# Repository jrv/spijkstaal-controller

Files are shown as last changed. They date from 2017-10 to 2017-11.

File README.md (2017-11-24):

# spijkstaal-controller
DC motor controller, 3-5KW / 24V

Experimental design for a replacement motor controller for a 1980's Spijkstaal electric vehicle.
This design is made in KiCad

Designed for a 24V Lead-Acid battery and a 3KW, 24V DC motor

Traditional H-bridge design with an Arduino as controlling interface.
The high power print and the controller print are seperate.

Carefull, this is work in progress. As it is now, it's sure to give you 
spectacular fireworks, but no moving vehicle!

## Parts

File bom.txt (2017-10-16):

BOM Mosfet board
================
8 x bout, 16x moer, 24xring M6 (€30,- montagetechniek.nl)
4 x 10K of 100K weerstand (naar 0 trekken)
1 x  RS 189-6256
1 x  RS 189-6060
12 x PSMN3R4-30PL Mosfet
5 x IDP30E65D1XKSA1
1 x Pudenz 425A Automotive Bolt-down Fuse, 80V dc
2 x 2200uF / 35V Elco
12 x Weerstand 4.7 ohm, 1/2Watt

BOM Arduino board
=================
Pin headers (arduino)
2 x DIP 2x8 voet
2 x 4u7 / 60V
5 x 100uF
1 x 7805
1 x 2200uF
1 x 1N4007
1 x RS 820-1576 pin header
1 x RS 820-1633 connector housing
1 x 7815ACT
2 x 1N5819
2 x IR2184
1 x Fuse holder RS  176-9047

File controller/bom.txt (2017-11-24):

Farnell:

2325975		1x	Fast / Ultrafast Diode 600V, 200A	23,38
2784061		4x	IXFN360N10T BJT MostFet 360A/100V	19,10
		    4x  Infineon IDP30E65D1 Disode 
2762031		1x	Fuse 150A 				14,34
2468299		2x	Condensator 2200 uF/100V		 3,13

RS: 
784-6229	1x	MagnaChip Dual Diode 400V 200A		19,43
125-8041	4x	IXFN360N10T BJT MostFet 360A/100V	18,77
787-4394	1x	LittleFuse 150A 32V fuse		 6,19
744-1183	2x 	Condensator 2200 uF/100V		 3,79

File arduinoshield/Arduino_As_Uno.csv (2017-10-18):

Id | Designator | Package | Quantity | Designation | Supplier and ref
1 | P1 | Socket_Strip_Arduino_1x08 | 1 | Power
2 | P2 | Socket_Strip_Arduino_1x06 | 1 | Analog
3 | P3 | Socket_Strip_Arduino_1x10 | 1 | Digital
4 | P4 | Socket_Strip_Arduino_1x08 | 1 | Digital
5 | P5,P6,P7,P8 | Arduino_1pin | 4 | CONN_01X01
6 | C6,C8 | CP_Radial_D5.0mm_P2.00mm | 2 | 4u7
7 | F1 | Fuseholder5x20_horiz_open_Schurter_0031_8201 | 1 | 1A
8 | R2,R4,R5 | R_1206_HandSoldering | 3 | 10K
9 | R3 | R_1206_HandSoldering | 1 | 4K7
10 | C1 | CP_Radial_D13.0mm_P5.00mm | 1 | 2200uF
11 | C2,C4,C5,C7,C9 | C_1206_HandSoldering | 5 | 100nF
12 | D1 | D_2114 | 1 | MRA4007T3G
13 | D2,D3 | D_SOD-123 | 2 | 1N5819HW-7-F
14 | U1 | ATPAK-2 | 1 | MC7815BD2TR4G
15 | U2 | ATPAK-2 | 1 | L7805CD2T-TR
16 | U3,U4 | SOIC-8-N | 2 | IR2184SPBF
17 | J1 | JST_XH_B08B-XH-A_08x2.50mm_Straight | 1 | Conn_01x08
18 | J2 | JST_XH_B05B-XH-A_05x2.50mm_Straight | 1 | Conn_01x05
19 | J3,J4,J6,J7 | JST_XH_B02B-XH-A_02x2.50mm_Straight | 4 | Conn_01x02
20 | J5 | JST_XH_B03B-XH-A_03x2.50mm_Straight | 1 | Conn_01x03

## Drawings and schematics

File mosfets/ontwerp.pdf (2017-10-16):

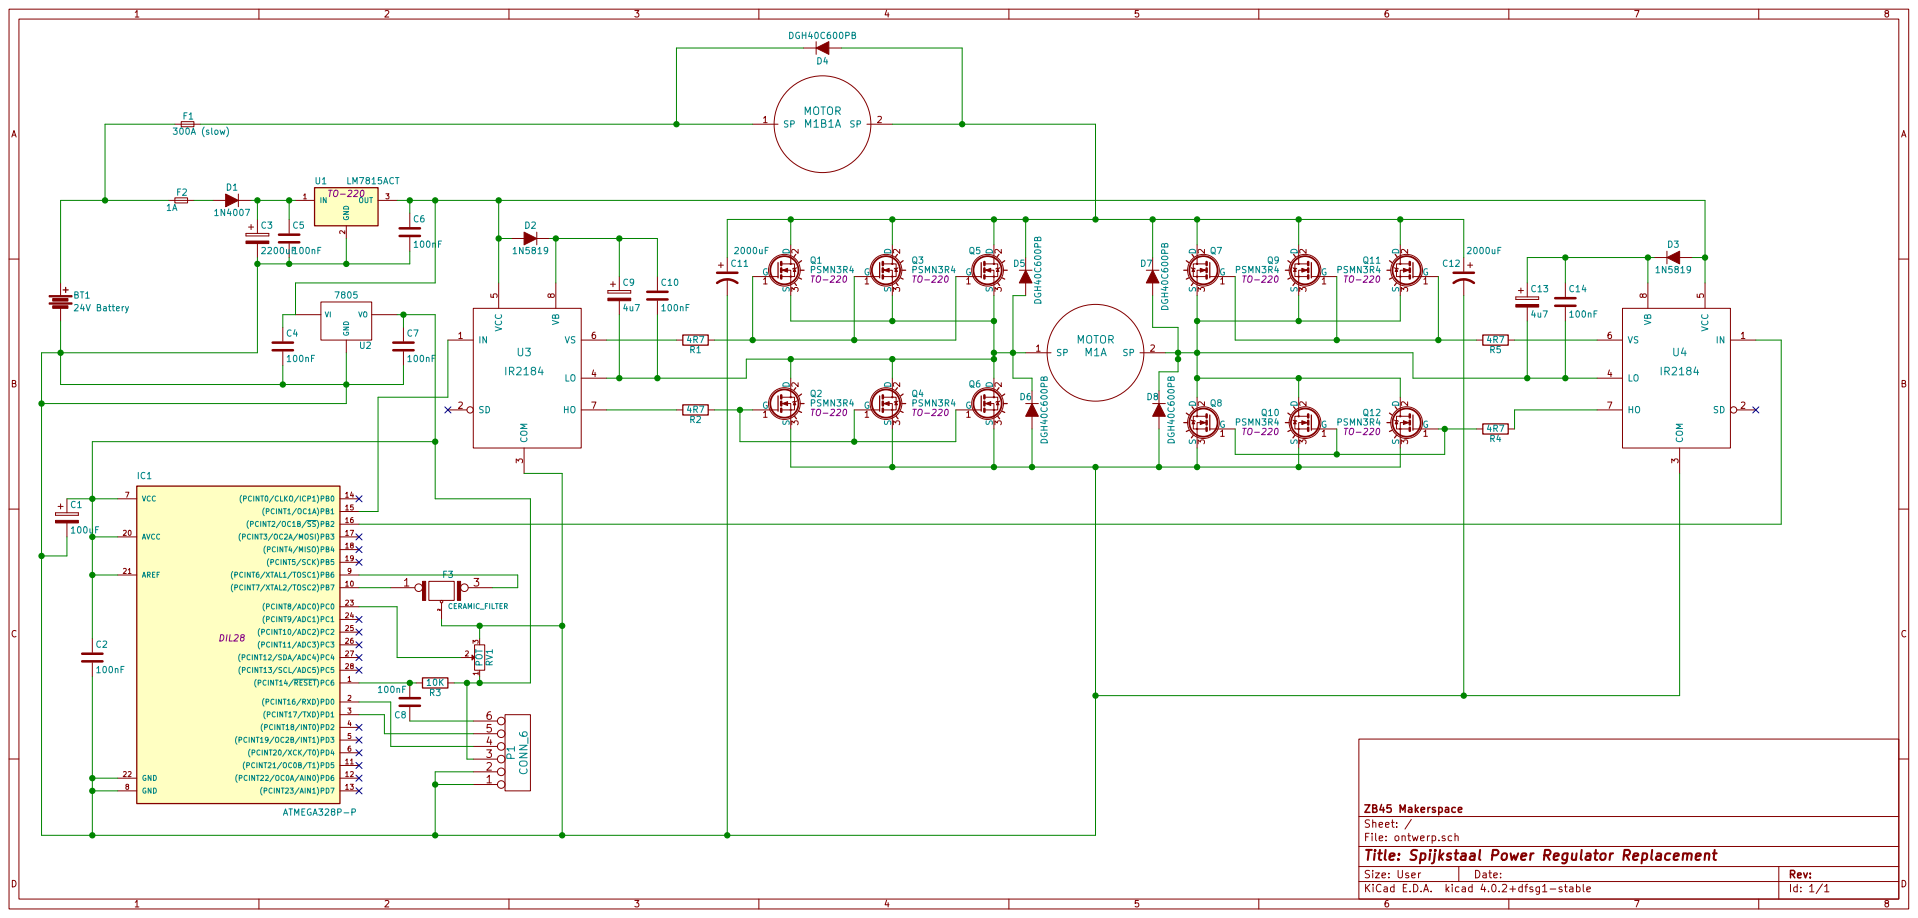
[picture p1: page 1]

File: ontwerp.sch Sheet: / ZB45 Makerspace

Id: 1/1 Title: Spijkstaal Power Regulator Replacement

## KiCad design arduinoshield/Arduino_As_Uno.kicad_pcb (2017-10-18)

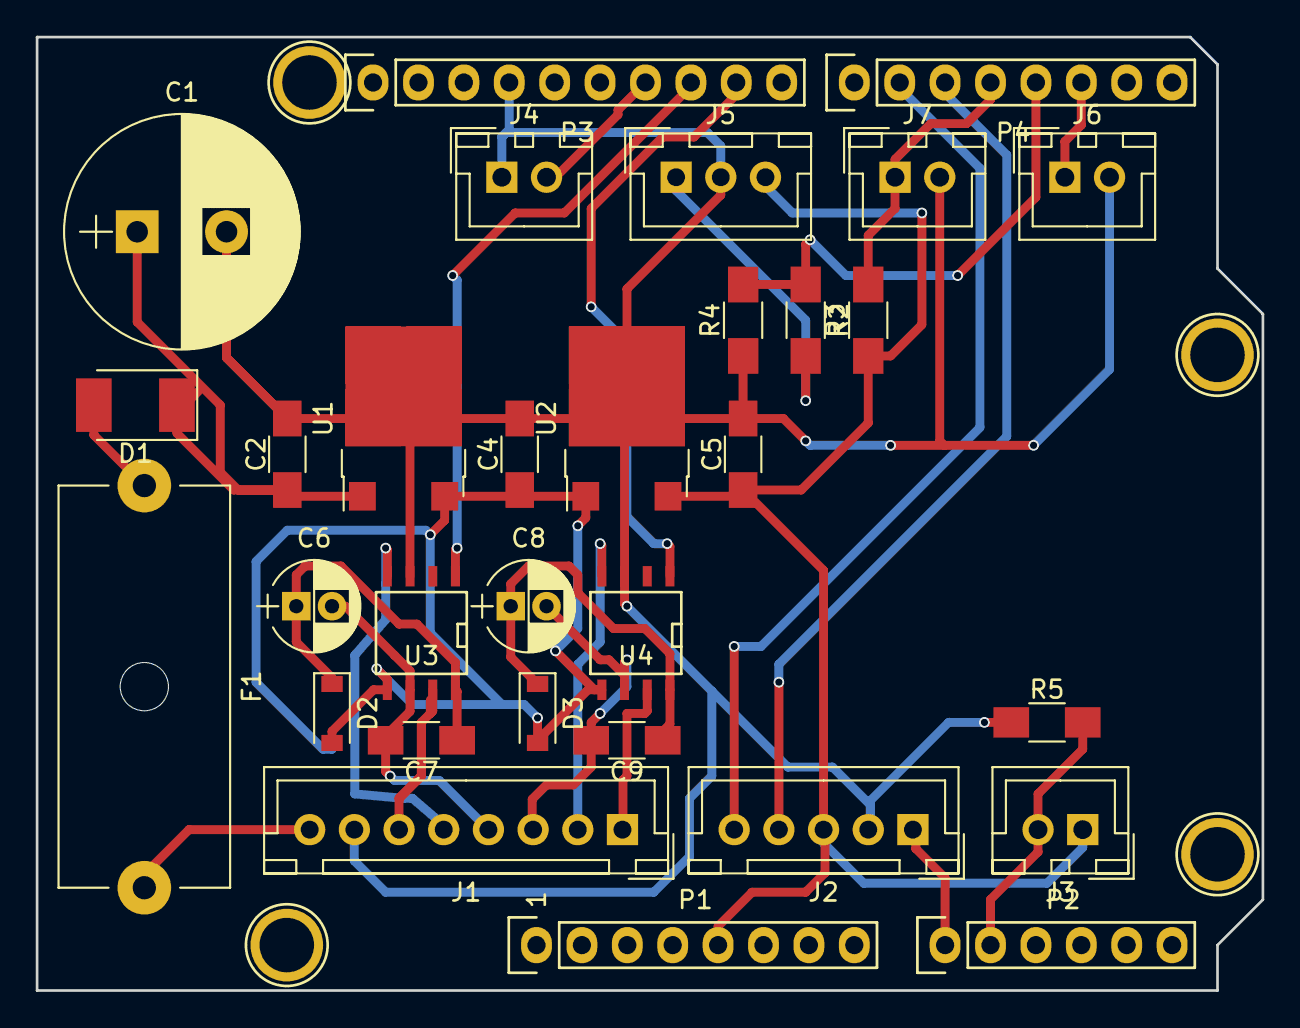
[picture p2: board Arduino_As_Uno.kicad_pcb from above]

Board: 2 copper layers, 68.6 x 53.3 mm, 35 parts (0 on the bottom side), 25 nets.

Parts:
C1: 2200uF; CP_Radial_D13.0mm_P5.00mm
C2, C4, C5, C7, C9: 100nF; C_1206_HandSoldering
C6, C8: 4u7; CP_Radial_D5.0mm_P2.00mm
D1: MRA4007T3G; D_2114
D2, D3: 1N5819HW-7-F; D_SOD-123
F1: 1A; Fuseholder5x20_horiz_open_Schurter_0031_8201
J1: Conn_01x08; JST_XH_B08B-XH-A_08x2.50mm_Straight
J2: Conn_01x05; JST_XH_B05B-XH-A_05x2.50mm_Straight
J3, J4, J6, J7: Conn_01x02; JST_XH_B02B-XH-A_02x2.50mm_Straight
J5: Conn_01x03; JST_XH_B03B-XH-A_03x2.50mm_Straight
P1: Power; Socket_Strip_Arduino_1x08
P2: Analog; Socket_Strip_Arduino_1x06
P3: Digital; Socket_Strip_Arduino_1x10
P4: Digital; Socket_Strip_Arduino_1x08
P5, P6, P7, P8: CONN_01X01; Arduino_1pin
R2, R4, R5: 10K; R_1206_HandSoldering
R3: 4K7; R_1206_HandSoldering
U1: MC7815BD2TR4G; ATPAK-2
U2: L7805CD2T-TR; ATPAK-2
U3, U4: IR2184SPBF; SOIC-8-N

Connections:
+5V: C5.1, J2.3, J3.1, J5.3, P1.5, R3.1, U2.3
/2: J6.1, P4.6
/3(**): P4.5, R2.1, R4.2
/4: J7.1, P4.4, R3.2
/5(**): J2.4, P4.3
/6(**): J2.5, P4.2
/9(**): P3.9, U4.1
/10(**/SS): P3.8, U3.1
/11(**/MOSI): J4.2, P3.7
/24V-Fused: D1.2, F1.1
/+15V: C4.1, D2.2, D3.2, U1.3, U2.1, U3.5, U4.5
/A0: J2.1, P2.1
/A1: J3.2, P2.2, R5.2
GND: C1.2, C2.2, C4.2, C5.2, J1.7, J2.2, J4.1, J5.2, J6.2, J7.2, P1.6, P1.7, P3.4, R4.1, R5.1, U1.2, U2.2, U3.3, U4.3
unnamed: C1.1, C2.1, D1.1, U1.1
unnamed: C6.1, C7.1, D2.1, U3.8
unnamed: C6.2, C7.2, J1.4, U3.6
unnamed: C8.1, C9.1, D3.1, U4.8
unnamed: C8.2, C9.2, J1.3, U4.6
unnamed: F1.2, J1.8
unnamed: J1.1, U4.7
unnamed: J1.2, U4.4
unnamed: J1.5, U3.4
unnamed: J1.6, U3.7
unnamed: J5.1, R2.2

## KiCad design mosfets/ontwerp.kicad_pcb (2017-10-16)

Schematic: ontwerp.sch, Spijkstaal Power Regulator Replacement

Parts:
BT1: 24V Battery; AccuDraad
C11, C12: 2000uF; CP_Radial_D22.0mm_P10.00mm_SnapIn
D4, D5, D6, D7, D8: D; TO-220-2_Vertical
F1: 300A (slow); BoltDownFuse
J1: Conn_01x08; PhoenixContact_MC-G_08x5.08mm_Angled
M1, M1B1: MOTOR; AccuDraad
Q1, Q2, Q3, Q4, Q5, Q6, Q7, Q8, Q9, Q10, Q11, Q12: PSMN3R4; TO-220
R1, R2, R4, R5, R6, R7, R8, R9, R10, R11, R12, R13: 4R7; R_Axial_DIN0309_L9.0mm_D3.2mm_P15.24mm_Horizontal

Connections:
/+24V: D4.1, F1.2, J1.1, M1B1.1
/+24V-NF: BT1.1, F1.1
/GND: BT1.2, C11.2, C12.2, D6.2, D8.2, J1.2, Q2.3, Q4.3, Q6.3, Q8.3, Q10.3, Q12.3
/M1: D5.2, D6.1, J1.5, M1.1, Q1.3, Q2.2, Q3.3, Q4.2, Q5.3, Q6.2
/M2: D7.2, D8.1, J1.6, M1.2, Q7.3, Q8.2, Q9.3, Q10.2, Q11.3, Q12.2
/M-IN: C11.1, C12.1, D4.2, D5.1, D7.1, M1B1.2, Q1.2, Q3.2, Q5.2, Q7.2, Q9.2, Q11.2
/SIG1H: J1.3, R1.1, R7.1, R9.1
/SIG1L: J1.4, R2.1, R6.1, R8.1
/SIG2H: J1.8, R5.1, R10.1, R12.1
/SIG2L: J1.7, R4.1, R11.1, R13.1
unnamed: Q1.1, R1.2
unnamed: Q2.1, R6.2
unnamed: Q3.1, R7.2
unnamed: Q4.1, R8.2
unnamed: Q5.1, R9.2
unnamed: Q6.1, R2.2
unnamed: Q7.1, R5.2
unnamed: Q8.1, R4.2
unnamed: Q9.1, R10.2
unnamed: Q10.1, R11.2
unnamed: Q11.1, R12.2
unnamed: Q12.1, R13.2

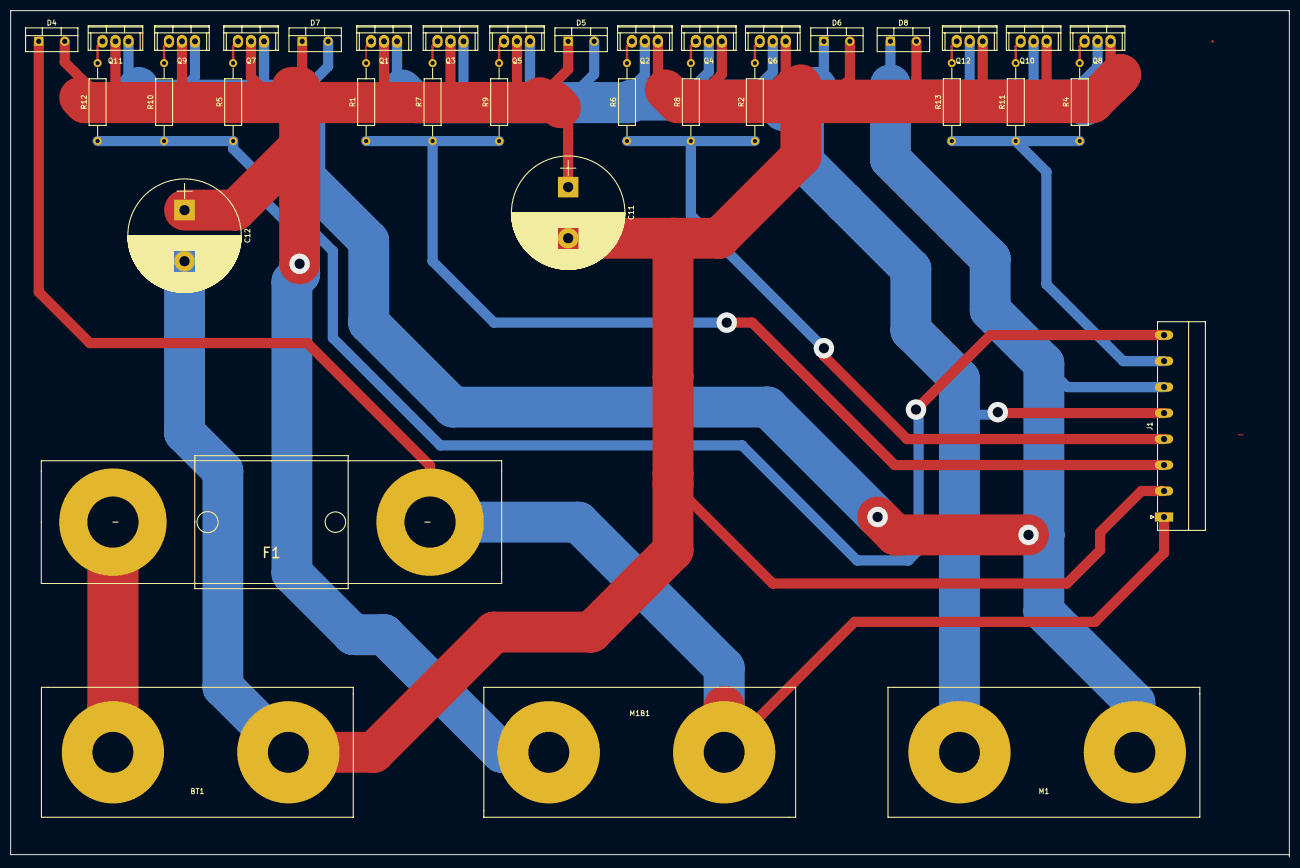
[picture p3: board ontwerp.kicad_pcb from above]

Board: 2 copper layers, 250.0 x 165.5 mm, 36 parts (0 on the bottom side), 22 nets.

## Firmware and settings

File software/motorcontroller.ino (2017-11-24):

//
// arduino program for spijkstaal controller
//
// A5 = gas pedal
// A1 = gearbox switch
int leftPin = 10;
int rightPin = 9;
int drivePin = 6;
int driveMaxPin = 5;
typedef enum Gear { reverse, neutral, forward };
Gear gear = neutral;
int maxSpeed = 150; // maximum pwm (between 0..254);
typedef enum speedMode { accel, steady, decel };
speedMode speedmode = steady;
int speed = 0;
#define DECEL 400
#define ACCEL 5000
int accelltime = 0;

// for later extensions:
// int TempPin = 8; // for oneWire protocol
// int SpeedoutPin = 11;
// int SpeedSensPin = 4;
// int Contact = 2;

void setup() {
  pinMode(leftPin, OUTPUT);
  analogWrite(leftPin,0);
  pinMode(rightPin, OUTPUT);
  analogWrite(rightPin,0);
  pinMode(drivePin, INPUT); // pullup?
  pinMode(driveMaxPin, INPUT); // pullup?
  Serial.begin(9600);
  Serial.println("Spijkstaal Controller started");
  accelltime = millis();
  // setPwmFrequency(9, 8);
  // setPwmFrequency(10, 8);
}

int speedVal() {
  bool drive = digitalRead(drivePin);
  bool driveMax = digitalRead(driveMaxPin);  
  int speedval = analogRead(A5);
  int res = 0;
  //Serial.print(speedval);
  if (drive) {
    if ((driveMax) && (speedval > 550)) {
	    res=maxSpeed;
	  } else {
      if (speedval < 220) { speedval = 220; }
      if (speedval > 615) { speedval = 615; }
      res = map(speedval,220,615,0,maxSpeed);
	  }
  } else {
    res = 0;
  }
  //Serial.print(" out: ");
  //Serial.println(res);
  return res;
}

void adjustSpeed(int runPin) {
  int speedval = speedVal();
  if (speedval < speed) {	// we should decellerate
    speed--;
    analogWrite(runPin, speed);
	delayMicroseconds(DECEL);
	if (speedmode != decel) {
		speedmode = decel;
		Serial.println("Decellerating");
	}
  }
  if (speedval > speed) {   // we should accellerate
    speed++;
    analogWrite(runPin, speed);
	delayMicroseconds(ACCEL);
  	if (speedmode != accel) {
		speedmode = accel;
		Serial.println("Accellerating");
	}
  }
  if (speedval == speed) { // we are running steady
  	if (speedmode != steady) {
		speedmode = steady;
		Serial.print("Steady: ");
    Serial.println(speed);
    Serial.print("in ");
    double res = (millis()-accelltime)/1000.0;
    Serial.print(res);
    Serial.println(" seconds");
    accelltime = millis();
	}
  }
}

Gear gearSwitch() {
  int dval = analogRead(A1);
  Gear newdir = neutral;
  if (dval > 400) newdir = forward;
  if (dval > 800) newdir = reverse;
  return newdir;
}

void loop() {
  switch (gear) {
    case neutral:  // Gear is in neutral
	  analogWrite(leftPin, 0);
	  analogWrite(rightPin, 0);
    speed=0;
    Serial.println("Neutral");
	  while (gearSwitch() == neutral);
	  gear = gearSwitch();
	  break;
	case forward: // driving forward
    speed=0;
    Serial.println("Forward");
	  while (gearSwitch() == forward) {
	    adjustSpeed(leftPin);
	  }
	  gear = neutral;
	  break;
	case reverse: // driving backwards
    speed=0;
      Serial.println("Reverse");
	  while (gearSwitch() == reverse) {
	    adjustSpeed(rightPin);
	  }
	  gear = neutral;
	  break;
  }
}

void setPwmFrequency(int pin, int divisor) {
  byte mode;
  if(pin == 5 || pin == 6 || pin == 9 || pin == 10) {
    switch(divisor) {
      case 1: mode = 0x01; break;
      case 8: mode = 0x02; break;
      case 64: mode = 0x03; break;
      case 256: mode = 0x04; break;
      case 1024: mode = 0x05; break;
      default: return;
    }
    if(pin == 5 || pin == 6) {
      TCCR0B = TCCR0B & 0b11111000 | mode;
    } else {
      TCCR1B = TCCR1B & 0b11111000 | mode;
    }
  } else if(pin == 3 || pin == 11) {
    switch(divisor) {
      case 1: mode = 0x01; break;
      case 8: mode = 0x02; break;
      case 32: mode = 0x03; break;
      case 64: mode = 0x04; break;
      case 128: mode = 0x05; break;
      case 256: mode = 0x06; break;
      case 1024: mode = 0x07; break;
      default: return;
    }
    TCCR2B = TCCR2B & 0b11111000 | mode;
  }
}

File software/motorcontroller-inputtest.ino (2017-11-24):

//
// input testing sequence
// arduino program for spijkstaal controller
//
// A5 = gas pedal
// A1 = gearbox switch
int drivePin = 6;
int driveMaxPin = 5;
typedef enum Gear { reverse, neutral, forward };
int maxSpeed = 255;

void setup() {
  pinMode(drivePin, INPUT); // pullup?
  pinMode(driveMaxPin, INPUT); // pullup?
  Serial.begin(9600);
  Serial.println("Spijkstaal Controller testing sequence started");
}

Gear gearSwitch() {
  int dval = analogRead(A1);
  Serial.print("Gear input: ");
  Serial.println(dval);
  Gear newdir = neutral;
  if (dval > 400) newdir = forward;
  if (dval > 800) newdir = reverse;
  return newdir;
}

void loop() {
  switch (gearSwitch()) {
    case neutral:  // Gear is in neutral
      Serial.println("Gear: Neutral");
	  break;
	case forward: // driving forward
      Serial.println("Forward");
	  break;
	case reverse: // driving backwards
      Serial.println("Reverse");
	  break;
  }
  bool drive = digitalRead(drivePin);
  bool driveMax = digitalRead(driveMaxPin);  
  int speedval = analogRead(A5);
  Serial.print("Speedval: ");
  Serial.println(speedval);
  Serial.print("Drive pin: ");
  if (drive) Serial.println("ON"); else Serial.println("OFF");
  Serial.print("DriveMax pin: ");
  if (driveMax) Serial.println("ON"); else Serial.println("OFF");
  if (drive) {
    if ((driveMax) && (speedval > 550)) {
	    speedval=maxSpeed;
	  } else {
      speedval = map(analogRead(A5),220,615,0,maxSpeed);
	  }
  } else {
    speedval = 0;
  }
  Serial.print("Speedsetting: ");
  Serial.println(speedval);
  Serial.println();
  Serial.println();
  delay(5000);
}

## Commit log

2017-10-16 Added mosfet design
    [ontwerp.kicad_pcb, ontwerp.sch]
2017-10-16 Added arduino shield v1
    [Arduino_As_Uno.kicad_pcb, Arduino_As_Uno.sch]
2017-10-16 Casing Mosfet part
2017-10-16 Cooler block for Mosfets & Diodes
2017-10-16 bill of materials
2017-10-18 redesigned arduino shield for with connectors and smd parts
    [Arduino_As_Uno.csv, Arduino_As_Uno.kicad_pcb, Arduino_As_Uno.sch]
2017-11-24 New controller design
    [Arduino_As_Uno.sch, controller.sch]
